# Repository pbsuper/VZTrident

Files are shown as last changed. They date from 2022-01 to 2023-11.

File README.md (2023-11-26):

# VZTrident
VZTrident the VZbot Trident child.

These builds are all VZbot sizes with triple Z sytem if you prefer Trident Z or Ratrig Style we have it both:

VZbot Gantry and tophat hinges.

Trident Skirt

Annex engineering Panel clips and Door Hinges for the 400 and 330 size.

Triple Z system inspired by the Trident and Ratrig.

Video of the 400 size printer: [VZTrident](https://drive.google.com/file/d/1hXe_eZGZ0fsk1MWA-nmpsxVc_xzYL8Yt/view?usp=sharing)

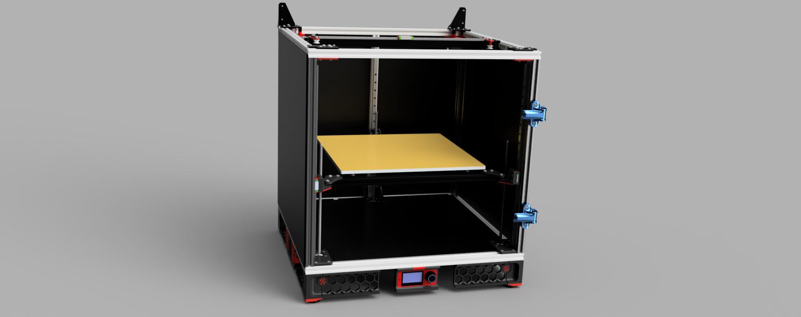
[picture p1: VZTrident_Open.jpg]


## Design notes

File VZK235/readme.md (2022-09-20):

Here's the VZK235AWD.

Using a Magnet and Balls Style Z with a awesome VZBot Skirt.

All files are included even a complete DXF set for the panels.

[Bom](https://docs.google.com/spreadsheets/d/1xvMW6YaFaoX6A90eS0pwF839IJyR271-2l1dd-D7zmQ/edit?usp=sharing)

[CAD](https://a360.co/37REtGY)
[CAD editable](https://drive.google.com/file/d/1RfbHU0f-XCdsnAkHNe-j8OYhcVrjgxWS/view?usp=sharing)

[Old VZT235 CAD](https://drive.google.com/file/d/1L4_Lsns9DV76UcdvgPYfmUujuNi_xPrc/view?usp=sharing)
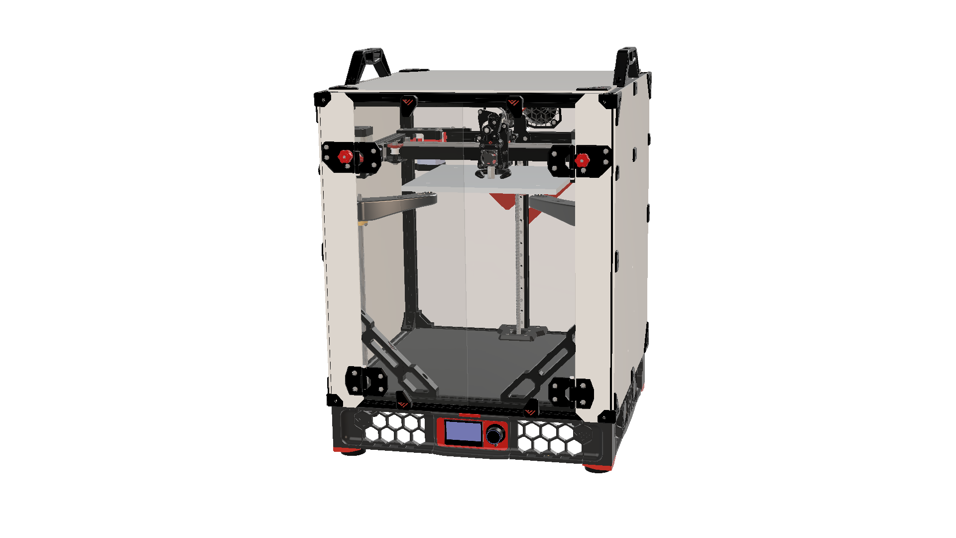
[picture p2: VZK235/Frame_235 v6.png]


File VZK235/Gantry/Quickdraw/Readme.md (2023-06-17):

Quickdraw mount for VZbot Alu Printhead.

Quickdraw 1 is the original older version. We have since updated to Quickdraw 2 and i would recommend everyone to use that.

Strip 2 24AWG wires for about 2cm twist the wire so no strands are loose and stick it in the back of the Quickdraw mount. Cut wires flush with magnets after they have been added into the mount and put a dot of glue on the wire where it enters the Quickdraw Mount. For added security you can add a tiny dot of solder onto the wire/magnet where they touch. be carefull not to heat the magnet since it will loose it's strength then.

The printed Printhead version is made for the backplate without tensioners. If you still tension your belts at the backplate this won't fit.

QD1 BOM
```
6x3mm Magnets 6x
M3 Heat inserts 8x
15cm 24AWG wire 2x
M2x10mm socket head NOT RVS/Stainless. Needs to be attracted to magnets.
Omron D2F-5 1x
```

QD2 BOM
```
6x6mm Magnets 4x
M3 heat inserts 4x
M3 Nut 1x
15cm 24AWG wire 2x
Omron D2F-5 1x
6x3-3mm ring magnets 2x [ring magnet](https://www.aliexpress.com/item/1005003026319118.html?)
M3x8mm Ultra Flat Head bolt Black 2x [Ultra Flats](https://a.aliexpress.com/_uH3ne5)
M3x12mm Button head or Ultra flat head 1x
M2x10mm Self tapping Button head NOT RVS/Stainless. Needs to be attracted to magnets.
```

To use quickdraw a module needs to be added.

SSH into your Pi with a application like Putty and type:
```
cd ~/klipper/klippy/extras
wget https://raw.githubusercontent.com/cloakedcode/klipper/blob/work-annex-probe/klippy/extras/dockable_probe.py
sudo service klipper restart 
```
For more info go to [Quickdraw](https://github.com/Annex-Engineering/Quickdraw_Probe)
Credits to Annex-Engineering for designing it.

Example Config for VZTrident 400 on BTT Octopus board:
```
[dockable_probe]
pin: PG10
x_offset:                          26 # offset for microswitch x direction off nozzle
y_offset:                          56 # offset for microswitch y direction off nozzle
z_offset:                          6.42 # offset for microswitch in z height

samples:                           3
sample_retract_dist:               3 # this is so the machine has time for the switch to reset properly, especially with a higher retract speed
samples_result:                    median
samples_tolerance:                 0.04
samples_tolerance_retries:         3
speed:                             15 # do not go higher than 10mm/s, you will destroy the switch
lift_speed:                        20
z_hop:                             15.0

attach_speed:                      8
detach_speed:                      10
travel_speed:                      300

approach_position:		           380,380,25 #you need to set these on your own
detach_position:		           360,330    #you need to set these on your own
dock_position:            	       390,380,25 #you need to set these on your own
dock_retries:			           3

check_open_attach:                 True #checks to see if the probe is attached before moving the toolhead, if not retries to pick up the probe
auto_attach_detach:                True
```

Example Config for the VZ235 with BTT Octopus Board with QD2:
``` 
[dockable_probe]
pin: PG10
x_offset:                          26 # offset for microswitch x direction off nozzle
y_offset:                          56 # offset for microswitch y direction off nozzle
z_offset:                          6.42 # offset for microswitch in z height

samples:                           3
sample_retract_dist:               3 # this is so the machine has time for the switch to reset properly, especially with a higher retract speed
samples_result:                    median
samples_tolerance:                 0.04
samples_tolerance_retries:         3
speed:                             15 # do not go higher than 10mm/s, you will destroy the switch
lift_speed:                        20
z_hop:                             15.0

attach_speed:                      8
detach_speed:                      10
travel_speed:                      300

approach_position:		           162,220,20 #you need to set these on your own
detach_position:		           100,240,20 #you need to set these on your own
dock_position:            	       162,240,20 #you need to set these on your own
dock_retries:			           3

check_open_attach:                 True #checks to see if the probe is attached before moving the toolhead, if not retries to pick up the probe
auto_attach_detach:                True
``` 

You also need to use a Safe_Z_Home to let it know where to move to to home Z.

```
[safe_z_home]
home_xy_position: 200,200 # set this to the center of your bed.
speed: 200
z_hop:20
z_hop_speed: 30
```

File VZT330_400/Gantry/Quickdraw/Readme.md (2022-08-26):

Quickdraw mount for VZbot Alu Printhead.

Quickdraw 1 is the original older version. We have since updated to Quickdraw 2 and i would recommend everyone to use that.

Strip 2 24AWG wires for about 2cm twist the wire so no strands are loose and stick it in the back of the Quickdraw mount. Cut wires flush with magnets after they have been added into the mount and put a dot of glue on the wire where it enters the Quickdraw Mount. For added security you can add a tiny dot of solder onto the wire/magnet where they touch. be carefull not to heat the magnet since it will loose it's strength then.

The printed Printhead version is made for the backplate without tensioners. If you still tension your belts at the backplate this won't fit.

QD1 BOM
```
6x3mm Magnets 6x
M3 Heat inserts 8x
15cm 24AWG wire 2x
M2x10mm socket head NOT RVS/Stainless. Needs to be attracted to magnets.
Omron D2F-5 1x
```

QD2 BOM
```
6x6mm Magnets 4x
M3 heat inserts 5x
15cm 24AWG wire 2x
Omron D2F-5 1x
6x3-3mm ring magnets 2x [ring magnet](https://www.aliexpress.com/item/1005003026319118.html?)
M3x8mm Ultra Flat Head bolt Black 2x [Ultra Flats](https://a.aliexpress.com/_uH3ne5)
M3x12mm Button head or Ultra flat head 1x
M2x10mm socket head NOT RVS/Stainless. Needs to be attracted to magnets.
```

To use quickdraw a module needs to be added.

SSH into your Pi with a application like Putty and type:
```
cd ~/klipper/klippy/extras
wget https://raw.githubusercontent.com/Annex-Engineering/klipper/master/klippy/extras/dockable_probe.py
sudo service klipper restart 
```
For more info go to [Quickdraw](https://github.com/Annex-Engineering/Quickdraw_Probe)
Credits to Annex-Engineering for designing it.

Example Config for VZTrident 400 on BTT Octopus board:
```
[dockable_probe]
pin: PG10 #your probe pin goes here
x_offset: 26 # offset for microswitch x direction off nozzle
y_offset: 56 # offset for microswitch y direction off nozzle
#z_offset: 6.42 # offset for microswitch in z height
samples: 3
sample_retract_dist: 3 # this is so the machine has time for the switch to reset properly, especially with a higher retract speed
samples_result: median
samples_tolerance: 0.04
samples_tolerance_retries: 3
speed: 15 # do not go higher than 10mm/s, you will destroy the switch
lift_speed: 20

dock_position:             390,380, 25 #you need to set these on your own
safe_z_position:           200,200 #used the center of the bed for this
approach_position:		   380,380, 25 #you need to set these on your own
detach_position:		   360,330 #you need to set these on your own
attach_speed:              8
detach_speed:              10
travel_speed:              300
check_open_attach:         True #checks to see if the probe is attached before moving the toolhead, if not retries to pick up the probe
dock_fixed_z:              True # k series printers use a dock fixed in the z axis, this was off a K2
dock_retries:			   3
```

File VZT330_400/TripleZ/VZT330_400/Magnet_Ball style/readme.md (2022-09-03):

EXPERIMENTAL!!!!
this has not been tested yet. build on your own risk.

[Dowel_pins](https://www.ratrig.com/dowel-pin-3-0mm-x-35-0mm.html) 6x

[Magnet](https://www.ratrig.com/magnet-20-x-10-x-5mm-two-hole-m3-countersink-screws.html) 3x

[12mm_Balls](https://www.ratrig.com/steel-ball-12mm-threaded-m5.html) 3x

with 12mm balls an adapter is needed due to M5 hole in balls and M3 hole in Vzbot Bed.

[Adapter](https://nl.aliexpress.com/item/1005003252950334.html?) 3x Inside M3 outside M5 6mm long.

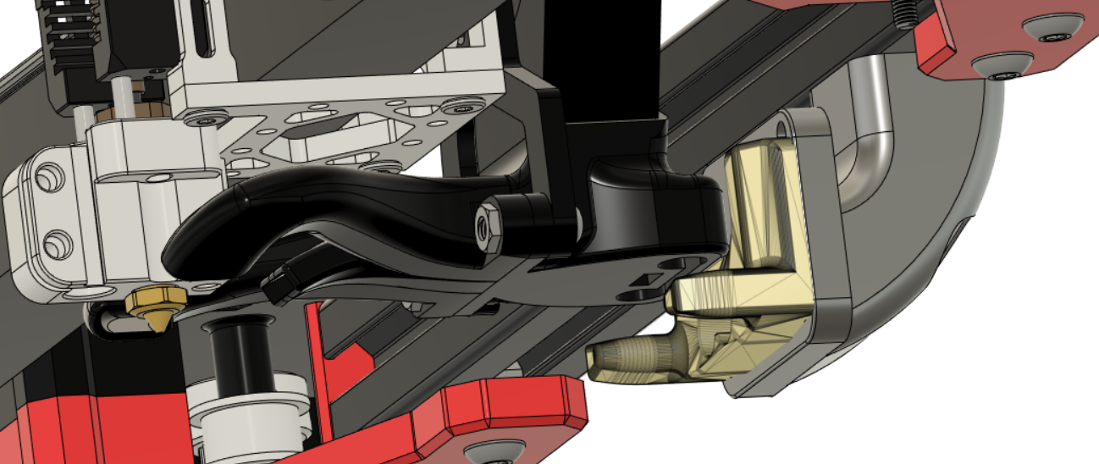
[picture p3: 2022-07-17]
VZT330_400/Gantry/Quickdraw/Quickdraw 2/overview2.png

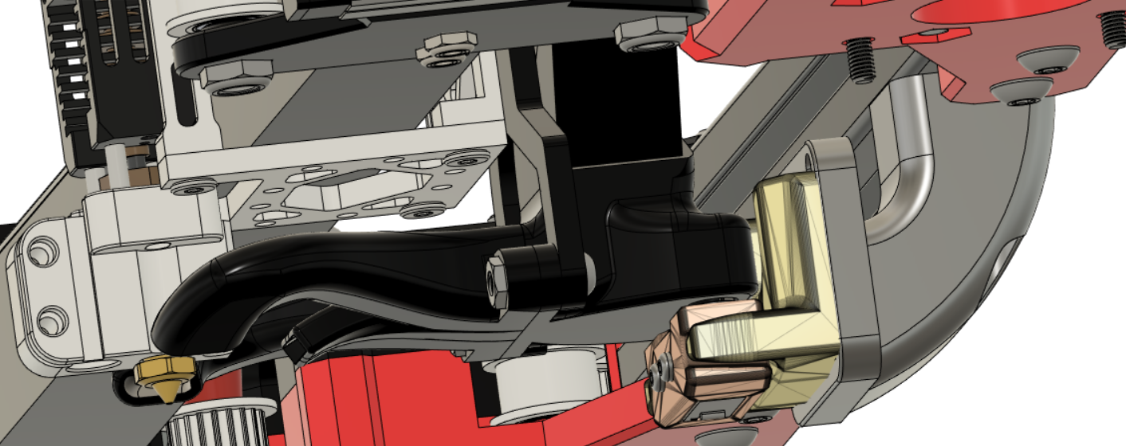
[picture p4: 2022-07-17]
VZT330_400/Gantry/Quickdraw/Quickdraw 2/overview.png

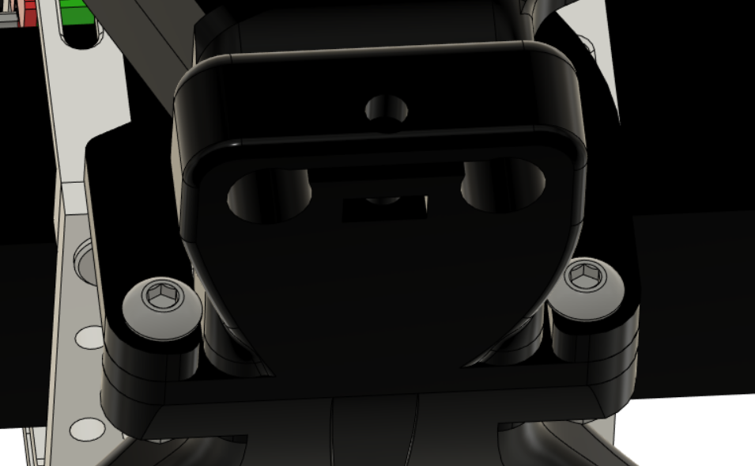
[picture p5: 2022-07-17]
VZK235/Gantry/Quickdraw/Quickdraw 2/overview3.png

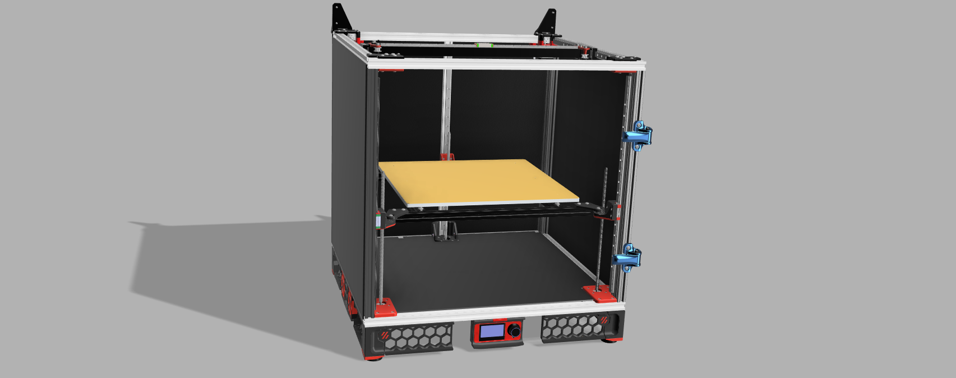
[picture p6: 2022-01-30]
VZTrident Inside.png

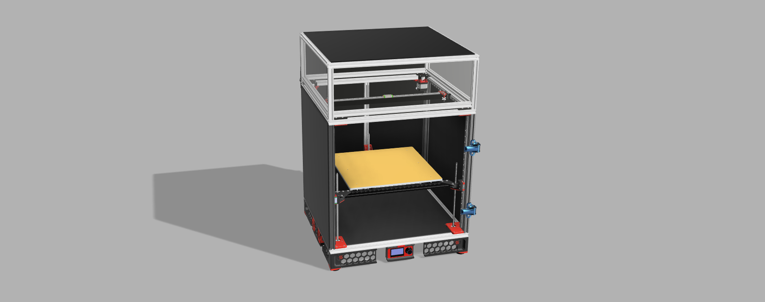
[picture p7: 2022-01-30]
VZTrident.png

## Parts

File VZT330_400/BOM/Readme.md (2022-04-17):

This is the Initial version of the BOM Everything is adapted to the 400 Size VZTrident Nuts and bolts have been added i've included some extra so you should have enough!

[BOM](https://docs.google.com/spreadsheets/d/1AV-jGdJS92EoAs13bpxHbbesQQFrgfEO-QNIa4KkuHc/edit?usp=sharing)

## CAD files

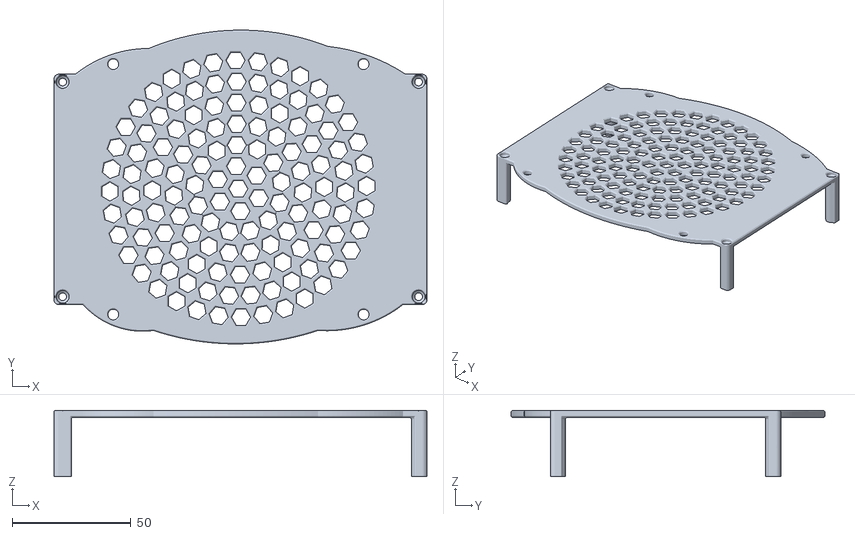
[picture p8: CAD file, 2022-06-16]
VZK235/Electronics/BTT_Octopus_V1.1_120mm_Fan_Mount.stl
157.2 x 132.2 x 28.0

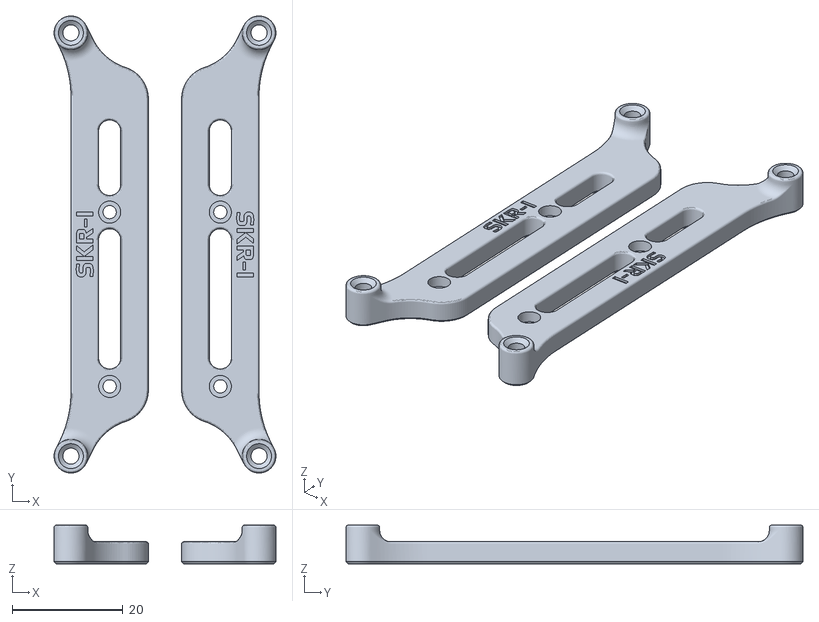
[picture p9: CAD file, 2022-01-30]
VZK235/Electronics/Controller_Mounts/SKR_bracket_inline_2pc.stl
40.1 x 82.6 x 7.00

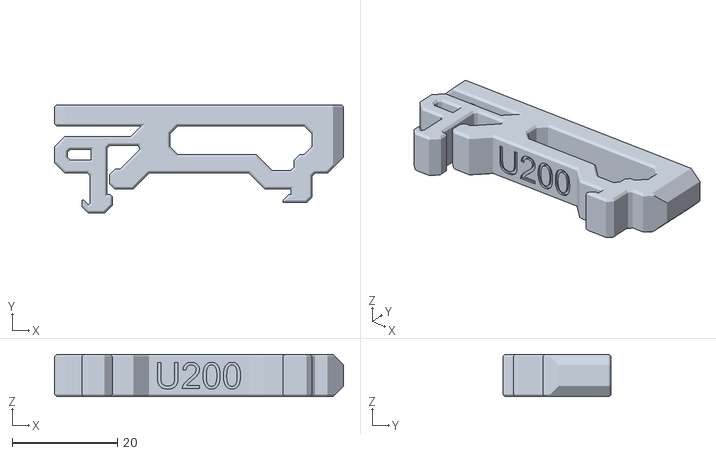
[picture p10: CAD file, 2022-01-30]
VZK235/Electronics/Other_PS_Mounts/UHP_200_Mount_x2.stl
55.0 x 20.6 x 8.00

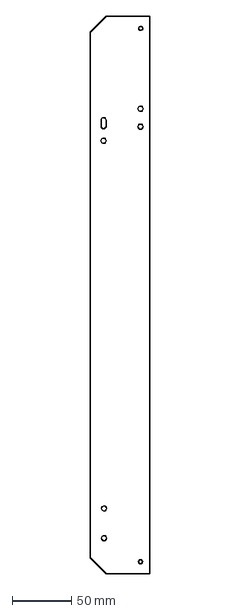
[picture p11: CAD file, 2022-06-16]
VZK235/enclosure/Panel_DXF/#Right_front_50mm.dxf
50.0 x 470.0 mm

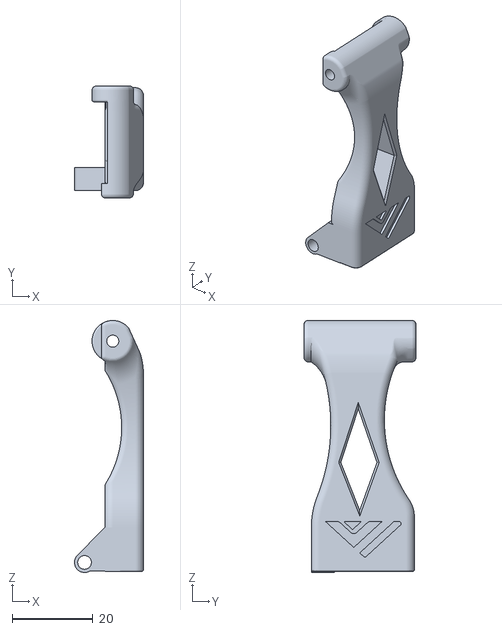
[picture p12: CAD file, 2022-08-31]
VZK235/Gantry/Quickdraw/Quickdraw 1/Quickdraw Mount_Printed_Printhead_Backplate_Tensioners.stl
17.2 x 27.8 x 62.6

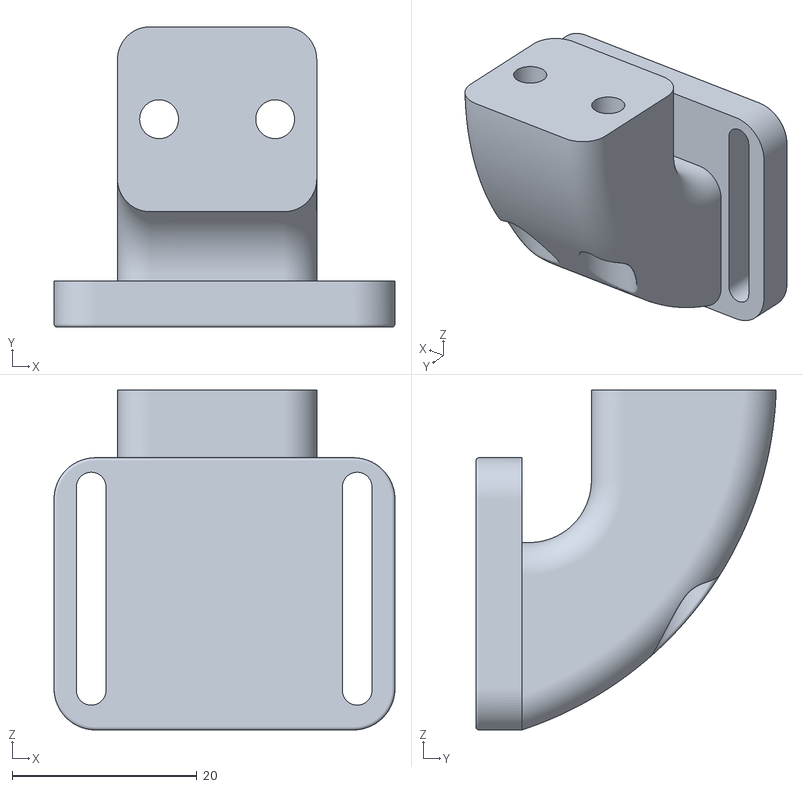
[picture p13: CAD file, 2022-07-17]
VZK235/Gantry/Quickdraw/Quickdraw 2/QD2_Dock_Mount.stl
36.9 x 32.5 x 36.8

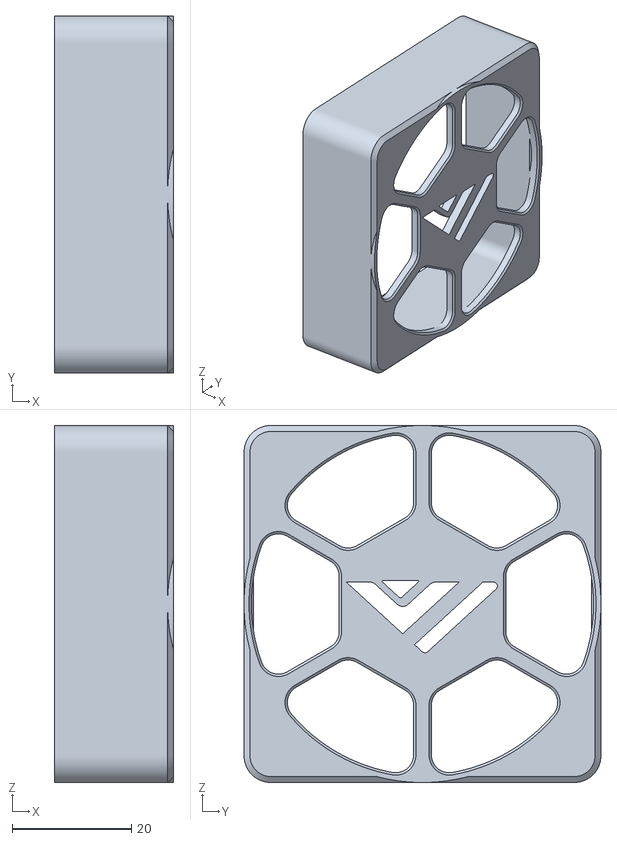
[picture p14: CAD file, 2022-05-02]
VZK235/Skirt/[a]_60mm_fan_blank_insert_x2.stl
20.0 x 60.0 x 60.0

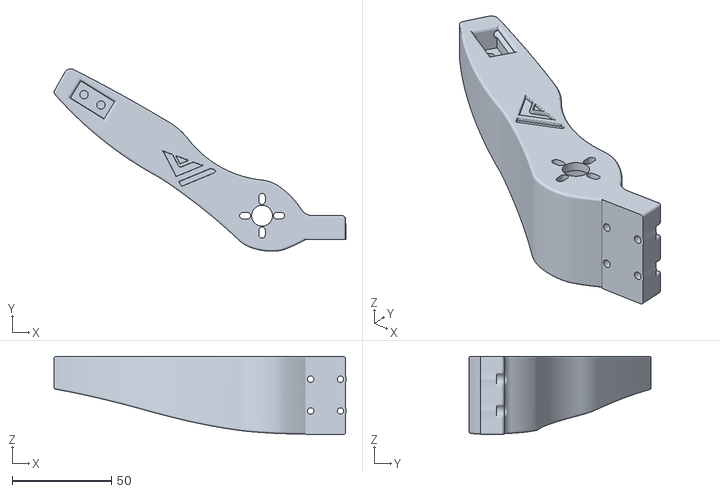
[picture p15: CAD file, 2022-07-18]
VZK235/Z-Assembly/Magnet_Balls_style/FR_K_Mount.stl
147.2 x 91.9 x 39.5

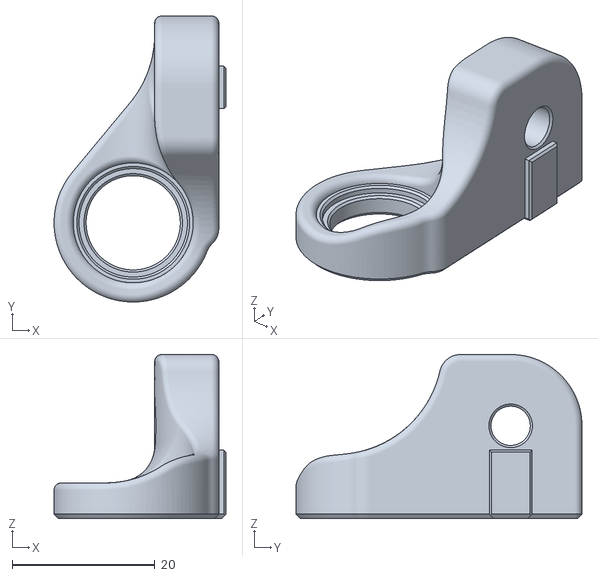
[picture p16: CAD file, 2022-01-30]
VZT330_400/Enclosure/front_door_bearing_block_1_x4_rev1.STL
24.1 x 40.1 x 23.0

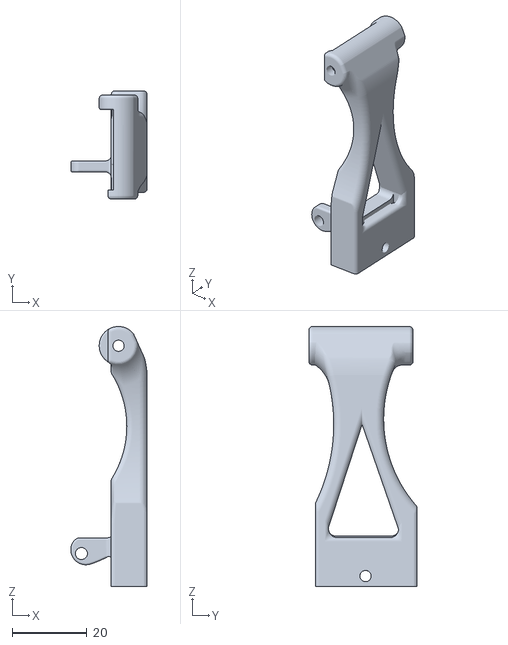
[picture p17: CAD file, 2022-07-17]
VZT330_400/Gantry/Quickdraw/Quickdraw_Mount_QD2_Rapido_UHF_Extender3mm.stl
20.4 x 28.9 x 69.3

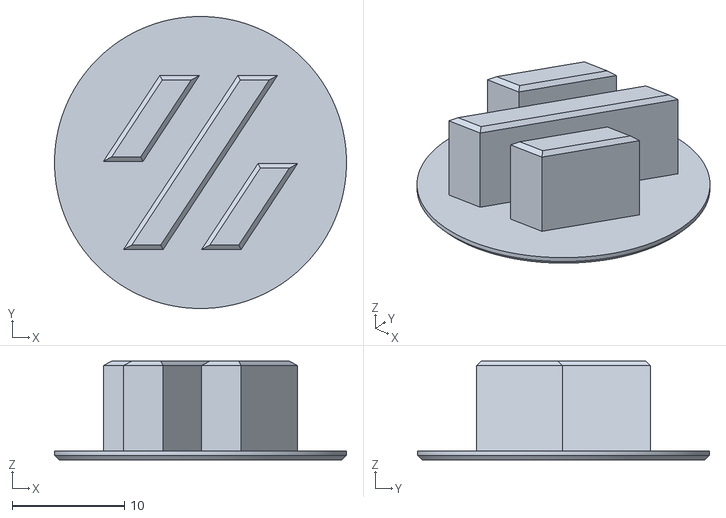
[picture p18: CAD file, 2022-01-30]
VZT330_400/Skirt/[a]_skirt_logo_x2.stl
26.0 x 26.0 x 8.80

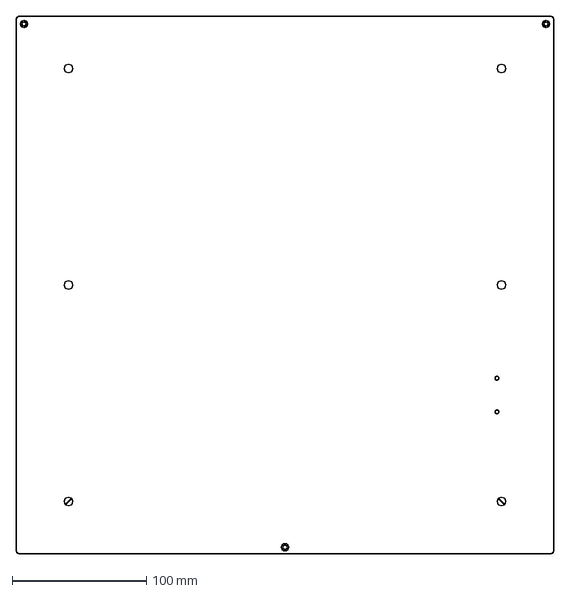
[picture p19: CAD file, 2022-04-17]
VZT330_400/TripleZ/400_bed_hole_locations.dxf
400.0 x 400.0 mm

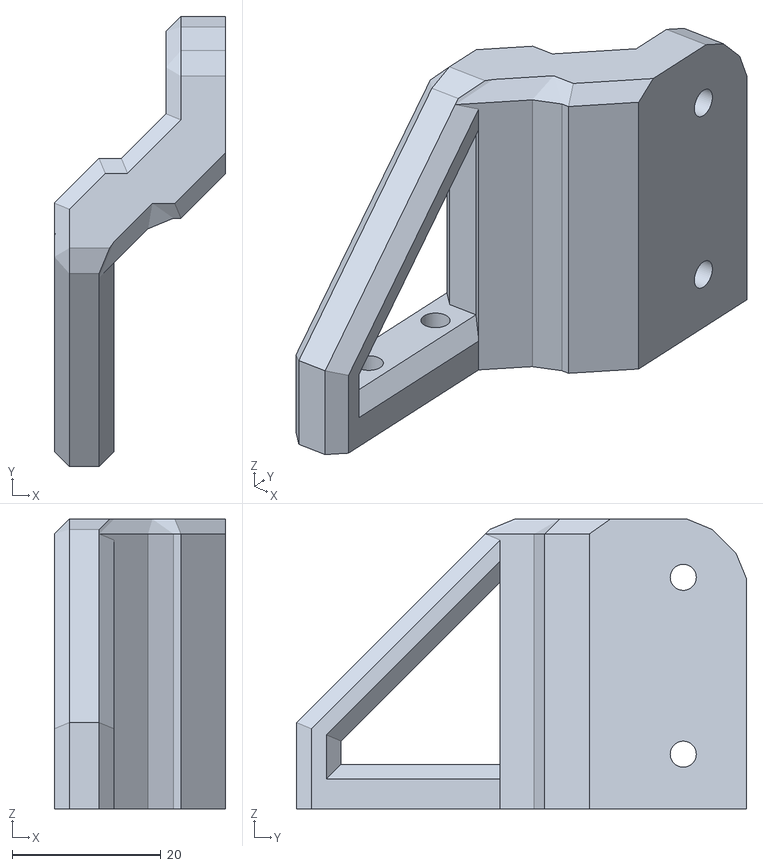
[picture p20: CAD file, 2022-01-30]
VZT330_400/TripleZ/VZT330_400/GE5C style/RM_L_Frame.stl
23.0 x 60.5 x 39.0

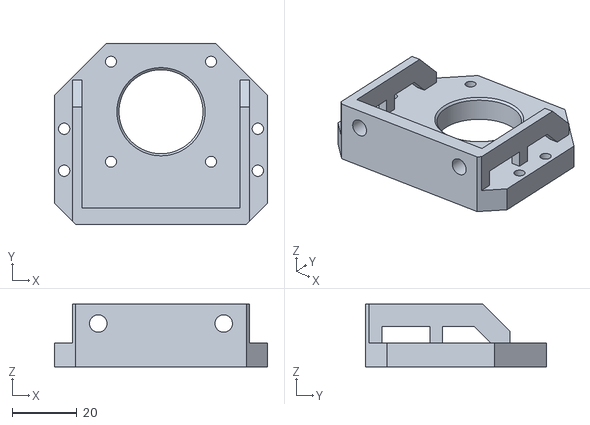
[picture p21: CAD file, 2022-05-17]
VZT330_400/TripleZ/VZT330_400/Magnet_Ball style/RM_Stepper_Plate.stl
66.0 x 56.0 x 19.4

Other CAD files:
VZT330_400/TripleZ/VZT330_400/Magnet_Ball style/VZ330/FR_K_Mount_MGN12H.stl
VZT330_400/TripleZ/VZT330_400/Magnet_Ball style/VZ400/RM_Magnet_Z_MGN12H.stl
VZK235/Electronics/Controller_Mounts/BTT_MOT_EXP_bracket.stl
VZK235/Electronics/Controller_Mounts/Duet2_Duet3Mini5_bracket_2pc.stl
VZK235/Electronics/Controller_Mounts/GTR_bracket_2pc.stl
VZK235/Electronics/Controller_Mounts/Octopus_bracket_2pc.stl
VZK235/Electronics/Controller_Mounts/SKR_DIN_mount.stl
VZK235/Electronics/Controller_Mounts/SKR_Pro_bracket_2pc.stl
VZK235/Electronics/Controller_Mounts/Spider_bracket_2pc.stl
VZK235/Electronics/DIN_center_support_x2.stl
VZK235/Electronics/DIN_frame_mount_x4.stl
VZK235/Electronics/DIN_frame_mount_x4_Wide.stl
VZK235/Electronics/Other_PS_Mounts/UHP_350_Mount_x2.stl
VZK235/Electronics/PSU_stabilizer_50mm.stl
VZK235/Electronics/cable_frame_anchor_x6.stl
VZK235/Electronics/lrs_psu_bracket_x2.stl
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

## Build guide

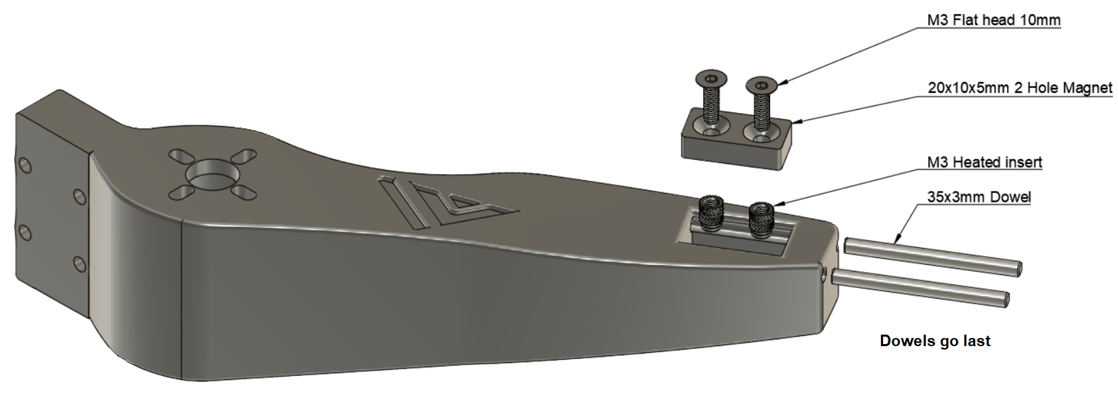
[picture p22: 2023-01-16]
VZK235/Z-Assembly/Magnet_Balls_style/Arm Assembly.png

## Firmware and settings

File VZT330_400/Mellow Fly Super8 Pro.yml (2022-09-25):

# the STM32F407 with a "32KiB bootloader".

[include mainsail.cfg]
[include Start_Stop.cfg]
[include Ztilt.cfg]
[include Adaptive_bedmesh_4.cfg]
#[include Sensorless_1.cfg]

[pause_resume]
[display_status]
[respond]
[virtual_sdcard]
path: ~/gcode_files

[stepper_x]
step_pin: PE2  # Drive0
dir_pin: PC5
enable_pin: !PF11
microsteps: 16
rotation_distance: 40
endstop_pin: tmc2209_stepper_x:virtual_endstop 
position_endstop: 0
position_max: 500
homing_speed: 50

#[stepper_x1]
#step_pin: PE3  # Drive1
#dir_pin: PF13
#enable_pin: !PF14
#microsteps: 16
#rotation_distance: 40

[stepper_y]
step_pin: PE4  # Drive2
dir_pin: PG0
enable_pin: !PG1
microsteps: 16
rotation_distance: 40
endstop_pin: tmc2209_stepper_y:virtual_endstop 
position_endstop: 0
position_max: 500
homing_speed: 50

#[stepper_y1]
#step_pin: PE14
#dir_pin: PE8
#enable_pin: !PE9
#microsteps: 16
#rotation_distance: 40

[stepper_z]
step_pin: PE15
dir_pin: PE11
enable_pin: !PF2
microsteps: 16
gear_ratio: 50:1
rotation_distance: 40
endstop_pin: probe:z_virtual_endstop
#position_endstop: 0.5
position_max: 350
homing_speed: 15
second_homing_speed: 3

[stepper_z1]
step_pin: PE1
dir_pin: PF0
enable_pin: !PC15
microsteps: 16
gear_ratio: 50:1
rotation_distance: 40 


[stepper_z2]
step_pin: PE0
dir_pin: PG3
enable_pin: !PG4
microsteps: 16
gear_ratio: 50:1
rotation_distance: 40 


[extruder]
step_pin: PE6
dir_pin: PG6
enable_pin: !PG7
microsteps: 16 
rotation_distance: 7.824
nozzle_diameter: 0.400
filament_diameter: 1.750
heater_pin: PB0 # Heat0
sensor_pin: PC1 # ADC_1
sensor_type: PT100 INA826
adc_voltage: 5.09
voltage_offset: 0
control: pid
pid_Kp: 22.2
pid_Ki: 1.08
pid_Kd: 114
min_temp: 0
max_temp: 500

[heater_bed]
heater_pin: PE5   # BED
sensor_pin: PF4   # ADC_5
sensor_type: ATC Semitec 104GT-2
control: watermark
min_temp: 0
max_temp: 200

# BLTouch port, has <GND>,<5V>,<CTRL>,<GND>,<PROBE>
[bltouch]
sensor_pin: ^PC3
control_pin: PC6
stow_on_each_sample: False
x_offset: 0 
y_offset: 0 
z_offset: 0
speed: 10
lift_speed: 25
samples: 3
sample_retract_dist: 5
samples_result: median
samples_tolerance: 0.03
samples_tolerance_retries: 3

[fan]
pin: PA0  # Fan0

[heater_fan fan1]
pin: PA1

#[heater_fan fan2]
#pin: PA2

#[heater_fan fan3]
#pin: PA3

#[heater_fan fan4]
#pin: PA15

#[heater_fan fan5]
#pin: PB11

#[heater_fan fan6]
#pin: PB10

#[heater_fan fan7]
#pin: PD12

#[heater_fan fan8]
#pin: PD14

#[heater_fan fan9]
#pin: PD15

[mcu]
serial: /dev/serial/by-id/usb-Klipper_stm32f407xx_410030000F47393436343431-if00

[printer]
kinematics: corexy
max_velocity: 300
max_accel: 3000
max_z_velocity: 5
max_z_accel: 100


[tmc2209 stepper_x]
uart_pin: PC4
run_current: 0.800
diag_pin: PG12
stealthchop_threshold: 0
interpolate: False
driver_SGTHRS: 80 # 255 is most sensitive value, 0 is least sensitive
driver_TBL: 1
driver_TOFF: 3
driver_HSTRT: 1
driver_HEND: 3

#[tmc2208 stepper_x1]
#uart_pin: PF12
#run_current: 0.800
#stealthchop_threshold: 999999
#diag1_pin: PG11

[tmc2209 stepper_y]
uart_pin: PF15
run_current: 0.650
diag_pin: PG10
stealthchop_threshold: 0
interpolate: False
driver_SGTHRS: 80 # 255 is most sensitive value, 0 is least sensitive
driver_TBL: 1
driver_TOFF: 3
driver_HSTRT: 1
driver_HEND: 3

#[tmc2208 stepper_y1]
#uart_pin: PE7
#run_current: 0.800
#stealthchop_threshold: 999999
#diag1_pin: PG9

[tmc2209 stepper_z]
uart_pin: PE10
run_current: 0.800
stealthchop_threshold: 999999
#diag1_pin: PD7

[tmc2209 stepper_z1]
uart_pin: PF1
run_current: 0.800
stealthchop_threshold: 999999
#diag1_pin: PD6

[tmc2209 stepper_z2]
uart_pin: PG2
run_current: 0.800
stealthchop_threshold: 999999
#diag1_pin: PA8

[tmc2209 extruder]
uart_pin: PG5
run_current: 0.800
stealthchop_threshold: 999999
#diag1_pin: PF3

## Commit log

2022-02-08 initial BOM
    [BOM.xlsx]
2022-04-16 Magnet_balls Z version
    GE5C method get's it's own folder
    Magnet/balls method added.
    Still experimental
    [FL_Bed_Mount.stl, FL_Magnet_Z_MGN12C.stl, FL_Rail_Ascent.stl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]
2022-04-16 added nuts and bolts
2022-04-17 10mm ball version
    [FL_Magnet_Z_10mm_MGN12C.stl, FL_Magnet_Z_MGN12C.stl, FL_Stepper_Mount.stl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]
2022-04-17 Magnet_balls update
    [400_bed_hole_locations.dxf, FL_Magnet_Z_10mm_MGN12C.stl, FL_Magnet_Z_MGN12C.stl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]
2022-04-17 Quickdraw
    added into Gantry folder.
    [Mount VZBot.stl, Mount_section_A_x1_Rev1 Edited.stl, Quickdraw Mount.stl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]
2022-04-18 adjusted print orientation
    [Mount_section_A_x1_Rev1 Edited.stl, Quickdraw Mount.stl, [a]_Magprobe_Dock_x1_Rev1 Edited.stl]
2022-04-23 Update Mount VZBot.stl
    [Mount VZBot.stl]
2022-04-27 MGN12H option
    [FL_Magnet_Z_10mm_MGN12H.stl, FR_Magnet_Z_10mm_MGN12H.stl, RM_Magnet_Z_10mm_MGN12H.stl]
2022-04-27 VZT235 Z
    Ratrig like Z added for VZ235
    [FL_Magbal.stl, FR_Magbal.stl, RM_Magbal.stl]
2022-05-01 Improved for no supports.
    [FL_Magbal.stl, FR_Magbal.stl, RM_Magbal.stl]
2022-05-01 ordening
    Split VZ235 and VZ330/400 in their own folders. Completed VZT235
    [400_bed_hole_locations.dxf, BTT_MOT_EXP_bracket.stl, DIN_center_support_x2.stl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]
2022-05-01 Enclosure added
    complete Enclosure and DXF files for every panel
    [Back_Panel.dxf, Bottom_panel.dxf, Duct v2.1 Straight.stl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]
2022-05-01 alu Y option added
    [1.4mm M5 spacer.stl, 11mm M5 spacer.stl, XendStop.stl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]
2022-05-09 fixed arms
    Bed was slightly in the wrong spot so arms had to be redesigned to regain all print space.
    [FL_Magbal.stl, FL_Magnet_Z_MGN12H.stl, FR_Magbal.stl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]
2022-05-12 parts updatet with logo
    [FL_Magnet_Z_MGN12C.stl, FL_Magnet_Z_MGN12H.stl, FR_Magnet_Z_MGN12C.stl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]
2022-05-22 Update Top_Panel.dxf
    updated for better use.
    [Top_Panel.dxf]
2022-06-12 Delete VZT330_400/TripleZ/VZT330_400/Magnet_Ball style/10mm Balls directory
    12mm balls easier to source and work better.
    [FL_Magnet_Z_10mm_MGN12C.stl, FL_Magnet_Z_10mm_MGN12H.stl, FR_Magnet_Z_10mm_MGN12C.stl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]
2022-06-16 removed 10mm ballls version
    [FL_Magnet_Z_MGN12C.stl, FL_Magnet_Z_MGN12H.stl, FR_Magnet_Z_MGN12C.stl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]
2022-07-17 Updated VZK330
    [FL_Bed_Mount.stl, FL_K_Mount_MGN12C.stl, FL_K_Mount_MGN12H.stl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]
2022-07-17 QD update
    [Mount VZBot.stl, Mount_section_A_x1_Rev1 Edited.stl, QD2_Dock_Mount.stl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]
2022-07-18 New arms
    [FL_K_Mount.stl, FL_Magbal.stl, FR_K_Mount.stl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]
2022-08-22 QD2 probe assembly
2022-08-22 QD2 assembly
2022-08-26 Update bolt link.
2022-08-31 old Quickdraw uploaded.
    [Quickdraw Mount_Printed_Printhead_Backplate_Tensioners.stl]
2022-09-25 Triple Z AWD Sensorless homing
